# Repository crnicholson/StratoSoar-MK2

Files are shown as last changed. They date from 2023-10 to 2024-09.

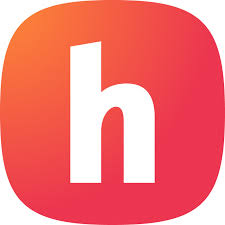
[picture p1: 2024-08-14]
Media/hack.jpeg

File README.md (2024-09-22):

# StratoSoar MK2 - UAVs For the Masses

<!-- **TL;DR**: The StratoSoar project is a low-cost, lightweight UAV designed to be dropped from a weather balloon  at any altitude, aiming for autonomous, efficient flight to selected GPS coordinates. The hope is to get a UAV platform in the hands of educators, researchers, and hobbyists alike since StratoSoar is much smaller, lighter, and cheaper than conventional UAVs.  -->

**TL:DR**: The StratoSoar project is a low-cost, lightweight Unmanned Aerial Vechile (UAV) designed for deployment from a weather balloon at various altitudes, aiming for autonomous and efficient flight to designated GPS coordinates. By offering a more affordable, compact, and lightweight alternative to conventional UAVs, StratoSoar aims to empower educators, researchers, and hobbyists with an accessible platform for exploration and experimentation. 

## Watch The Video

<!-- **WORK IN PROGRESS** - This project is still in the works. I don't recommend using it yet because it has the potential of being dangerous.

**NEW** - Writing code and making the PCB. 

**STATE as of 7/1/24** - Just starting development! -->

YouTube Video (https://www.youtube.com/watch?v=TiqkcGWG4g8&t=1s)

Glider | PCB
-- | --
<i>StratoSoar glider.</i> | <i>StratoSoar MK2.0 circuit board.</i>

## What Is the StratoSoar Project?

StratoSoar is a low-power, adaptive UAV that is dropped from a weather balloon at approximately 5,000 feet, with plans to reach even higher altitudes soon. The main goal of StratoSoar is to fly to selected GPS coordinates efficiently or choose a closer, more realistic landing site without human interaction. The current aim for StratoSoar is to operate on a single 600 mAh 15 gram LiPo battery for a 10+ hour flight. 

## Now, What Is a UAV?

UAVs, or Unmanned Aerial Vehicles, are autonomous aircraft, usually in the form of planes or drones. They have many applications, such as [delivering medicine, food, and supplies](https://www.flyzipline.com/) to remote areas, participating in aerial combat with the military, and conducting aerial imaging.

### Common Types of UAVs Include:

- Quadcopter (typical drones)
- Fixed-wing aircraft (like StratoSoar)

## StratoSoar vs. Conventional UAVs

### Traditional UAVs Are Typically:

- Large (5-15 meter wingspan)
- Heavy (2-20 kg)
- Expensive ($10,000-10,000,000 USD)
- Closed source and propietary

### StratoSoar Aims to Overcome These Limitations With:

- Weight: less than 250 grams
- Wingspan: 80 cm
- Cost: less than $150 USD
- Open source and accesible

## What Are the Uses of StratoSoar?

I'm currently considering two main concepts: an educational kit for students and hobbyists or a platform designed to study the aerodynamics of the stratosphere, a field with limited existing resources. Additionally, I'm exploring other ideas such as reusable radiosondes, systems for remote delivery of medicine and parcels, and advanced atmospheric monitoring solutions.

<!-- ## What Includes the StratoSoar Project? What Are the Different Parts of it?

StratoSoar has many different parts, and they all combine to make this project. 

- **Code** - All of the code directory, and the programs needed to run it. These include the main `.ino`s and the accompanying `.cpp` and `.h` files, along with the test files for the IMU and GPS.
- **PCB** - The circuit board is the basis of this project, it interfaces the code with the glider. StratoSoar includes the circuit board files and the schematics and everything needed to build a PCB.
- **3D Files** - StratoSoar requires some 3D printed parts to function, but these files also serve as an interactive build guide. StratoSoar includes the 3D files needed to print parts for the glider and the 3D files to assemble the glider.
- **Media** - The images and such of StratoSoar. 
- **Cutdown Mechanism** - This is the thing that helps you release the glider from the balloon payload - or whatever you want to drop it from. This includes all of the above things but will be in a separate GitHub repository.  -->

## How Does StratoSoar Work at a High Level?

<!-- StratoSoar is attached to a weather balloon via the cutdown mechanism. Once the balloon reaches the desired altitude, the cutdown mechanism drops the glider. The glider then descends, steering its way to specified coordinates. 

StratoSoar takes pride in being highly configurable and hackable, so there are many ways you change how it comes down built into the code. 

StratoSoar uses data from an IMU that goes through a Kalman filter to receive accurate AHRS, or Attitude Heading Reference System. This can tell StratoSoar the pitch, yaw, and roll of the glider. Then, StratoSoar integrates a GPS module to get the GPS coordinates. Both the GPS and the AHRS are used to compute the azimuth to find the turning angle of the glider. The turning angle tells the glider how much it needs to turn to be facing the correct yaw that will get the glider to the target location. Additionally, an algorithm is used to get the distance between the glider location's and the target location. 

With the turning angle computed, a PID mechanism is used to control the servo attached to the rudder of the glider. This PID mechanism learn from it's mistakes and can accurately aim the glider in the correct direction. 

Additionally, the glider beacons it's location at a configurable interval with LoRa for tracking. It also allows for a camera module to be added on to take photos and video. 

The glider will fly to the selected coordinates, and depending on the user configuration, will either spiral down or release a parachute above the coordinates once it has reached them to safely descend. Additionally, if the glider is too low in altitude, prior to the flight the user can enter closer coordinates as backup landing locations.  -->

StratoSoar MK2 is an advanced autonomous glider designed to operate at high altitudes, such as those reached by weather balloons. The glider is attached to a weather balloon via a cutdown mechanism. Once the balloon reaches the desired altitude, the cutdown mechanism releases the glider, initiating its descent. The glider then navigates autonomously to specified coordinates, using a combination of sensors, advanced algorithms, and low-power electronics.

### Core Components and Functionality:

- **Autopilot System**:
    - **GPS and IMU Integration**: StratoSoar uses a custom GPS module and an IMU, both designed for low-power operation. The IMU data is processed through a Kalman filter to provide accurate Attitude Heading Reference System (AHRS) data, including pitch, yaw, and roll. This information, combined with GPS coordinates, enables precise navigation.
    - **Servo Control with PID**: A PID control mechanism governs the rudder’s servo, ensuring precise adjustments to the glider's course based on real-time feedback.
    - **Hackability**: StratoSoar is designed to be highly configurable and hackable. Users can customize its descent strategy, whether by spiral descent, parachute deployment, or alternative landing locations. The codebase is modular, allowing for easy modifications or the addition of new features.
   
- **PCB Design**:
    - **StratoSoar MK3 PCB**: The main PCB, optimized for power efficiency, size, and cost, integrates over 100 components, managing the various systems onboard.
    - **Additional PCBs**: Supporting PCBs, such as those for the GPS module, switching regulator, and IMU, are designed for specific tasks, enhancing the glider's overall functionality.

### Operation and Recovery:

Upon release from the weather balloon, StratoSoar begins its guided descent following waypoints or single target coordinate. It calculates the optimal flight path using its GPS and AHRS data, making real-time adjustments to its trajectory through the PID-controlled servo system. Depending on user configurations, the glider can either glide smoothly to the target coordinates, initiate a spiral descent, or deploy a parachute for a safe landing.

If the glider's altitude drops below a certain threshold, backup landing coordinates can be used to ensure a safe recovery. Throughout the flight, the glider’s location is continuously transmitted, allowing for easy tracking and recovery.

<!-- ## File System and More Project Info

I'm only listing the key items, leaving out all the unessecary stuff. This should give you a general sense of the project and all it's features. Note that this is also only stuff I did during Hack Club Arcade.

- `Code/autopilot`: (5000 lines of code!)
    - `autopilot.ino`: The script that ties all of these files together.
    - `gps.cpp`: GPS code custom-made for low-power.
    - `waypoint.cpp`: Custom waypoint flight with advanced turning.
    - `lora.cpp`: LoRa communications with complex forward error correction.
    - `sd.cpp` + `eeprom.cpp`: Data logging in a low-power manner.
    - `servo.cpp`: Ultra low-power servo functions.
    - `bme280.cpp`: Weather data sensor.
    - `imu.cpp`: An interial measurement unit running a Kalman filter.
- `Code/groundStation`: 
    - `groundStation.ino`: The code for the receiving station of the LoRa telemetry, uses ESP32 and HTTP requests to communicate with the server, also locally logs data. 
    - `uploader/flaskUploader.py`: A Flask server that uses an API to put all the data on SondeHub. 
- `Code/camera`: Utilization of a low-power camera module and Python scripts for conversion.
- `Code/calculator`: Python script to parametrically create flying wing glider. 
- `PCB/StratoSoar-MK3.0`: The main PCB consisting of over 100 components, optimized for power, size, and cost.
- `PCB/gpsBreakout`: A PCB designed for testing a cheap, $2 Chinese GPS module.
- `PCB/loRa`: The ground station to receive the glider's data. 
- `PCB/camera`: A breakout board for a low-power camera module. 
- `PCB/imuBreakout`: One of the first breakout boards made for a new Interial Measurement Unit. 
- `3D Files/cardboardGlider`: Parametric Fusion 360 desgin for a folding origami glider. 
- `3D Files/StratoSoar Rev2 v36`: High efficieny glider. -->

## A Quick Note on MK1, MK2, Naming, and Revisions

StratoSoar MK1 was the precursor and the spark to StratoSoar MK2. StratoSoar MK1 was officially developed from October 1st to July 30th, although StratoSoar MK2 was unofficially being worked on in the months of March through June. StratoSoar MK1 failed to fly autonomously, and it also failed to release from the balloon. Major upgrades have been made since then.

StratoSoar MK2 officially started on October 1st, and has now ended. It was a success. 

My newer version, which you should check out, officially started on June 1st. It is called StratoSoar MK3 and will end in quite some time when I launch it from a weather balloon. A new major revision (eg. MK4) will come out every time when I release the glider from the balloon in the Summer. After the Summer, work on the next revision begins, with many updates and new features. 

<!-- A new sub-revision (for lack of better word) comes out every time I make a new PCB. For example, my first version of my PCB was MK2.0. At the time of writing, the current version of StratoSoar is MK2.1. A new version of 3D model is denoted by the Rev number. Rev starts at 0. 0 and 1 are not shown in this repo because they didn't turn out very good. The physical gliders are denoted by the 3D model number. Sometimes a small change is made with glider so the name of the glider is Rev x.x, for example. Sometimes the same happens with the 3D model, again it would be x.x. To put this in practice, the final glider may be MK2.5 Rev 7.3.1. The code has no version history in the way the 3D models and the PCB do. -->

Also, I use "we" a lot in this writing. This usually refers to myself or this project, but it also refers to my small team over at New England Weather Balloon Society.

One last thing. When I refer to StratoSoar, I am referring to the project as a whole, but more specifically, the most recent version. 

<!-- ## Watch my Talk About StratoSoar MK2 The North East HamXpo! -->

## Is This Legal?
Yes! During flight, the ground operator has no ***direct*** control over the flight path, i.e. via a radio. Because of this, and it being unpowered, it qualifies as a free flight glider. Free flight gliders have very little regulations. You can think of them as a paper airplane. 

## Can I Buy a Kit or a Complete Product?

Currently, StratoSoar is not available to purchase online as a kit or complete product. We have plans in the next few years to release a kit for schools, education centers, hobbyists and a complete product for industry at an affordable price. You are welcome to make one in the mean time!

## How Can I Make One? Are There Docs?

One of the goals of StratoSoar was to make an affordable and open source system for anyone to perform stratospheric research, so all the files are available for free. This means that you can construct StratoSoar from scratch. **A guide to do this will be available soon.**

<!-- It is still in the works, but you can check out `DOCS.md` under the `Docs` folder.**  -->

## Helpful Sources and Credits

I'm in the midst of compiling this.

## Cutdown Mechanism

[See my other WIP GitHub repo.](https://github.com/crnicholson/Cutdown-Mechanism)

## Funding and Support

We currently have <u>**very**</u> limited funding to complete this project. We would **love any donations or sponsorships** we could get to elevate (no pun intended) this project to the next level. If you don't want to donate, but want to help out, we would love your support with other areas of this project. Reach out to me if you have interest at:

- [newbsballoons@gmail.com](mailto:newbsballoons@gmail.com) (organization email, recommended).

- [charlienicholsonr@gmail.com](mailto:charlienicholsonr@gmail.com) (personal email).

## Special Thanks

This project would not be possible without the following individuals:

- Max Kendall (W0MXX) for working closely together with me.

- Mike Malis for helping with the design of the glider. 

- Brett Miwa for schematic review, PCB design, electrical theory, and boost converter circuitry design.

- Bob Phinney (K5TEC) for providing NEST and securing funding.

- Mark Jessop (VK5QI) for answering all of my questions.

- Mike Hojnowski (KD2EAT) for PCB design and hardware/software debugging.

- Paul Hamilton for helping me with FAA regulations.

- My parents!

And these entities:

- Hack Club, for providing support for projects like this. 

- New England Sci-Tech (NEST) for providing a maker space to work, funding, and hosting NEWBS.

- New England Weather Balloon Society (NEWBS) for expertise and the opportunity.

- Bagel Fund, for providing funding. 

## Affiliate Programs and Projects

- **Hack Club** - Hack Club is a non-profit designed for teenagers that provides support for projects like this. 
- **NEWBS** - Max and Seth Kendall of NEWBS, or New England Weather Balloon Society, are helping me launch my project from a balloon. They are dedicated to helping people in New England launch weather balloons. 
- **New England Sci-Tech** - Bob Phinney of NEST is hosting NEWBS. NEST is a great maker space. If you are in the Greater Boston Area, go check them out!
- **StratoScience** - This is the official class that I'm in helping me launch my project. This is a high altitude engineering class for teens. Check them out if your are in the Greater Boston area!

## Still Have Questions?

Do you have any questions? Are the docs incomplete and you want to ask anything? Do you just want to say hi (or how cool my project is!)?

Reach out to me at [charlienicholsonr@gmail.com](mailto:charlienicholsonr@gmail.com).

## License

Both the software and documentation are under the [GNU GPL v3 license](https://choosealicense.com/licenses/gpl-3.0/). The hardware and the 3D files are under the [CERN Open Hardware Licence Version 2 - Strongly Reciprocal](https://choosealicense.com/licenses/cern-ohl-s-2.0/). The media is under the [CC BY 4.0 DEED](https://creativecommons.org/licenses/by/4.0/).

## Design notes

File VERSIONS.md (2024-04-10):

## Version History

A quick little summary of the versions and what worked and what didn't, plus what was changed between revisions.

PCBs:
- StratoSoar MK2.0 - First attempt, many issues. Wrong LDO, transistor, and TCXO footprint. Boost converter did not work. Reset button did not work. Main sketch works along with mostly everything else. Missing silkscreen designators and numerous cosmetic problems. GPS untested. IMU untested.
- StratoSoar MK2.1 - Success!

Gliders/3D models:
- Rev 0 - Never flew, bad design.
- Rev 1 - Built and tested, horrible design.
- Rev 2 - Currently constructing this.

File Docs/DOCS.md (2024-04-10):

# StratoSoar Docs - A Work in Progress!

This is split into a few different sections to be more organized. These are as follows:

- General
- PCB
- Code and Programming
- Glider
- Usage

# General

## StratoSoar File Layout

## Power Consumption

# PCB

## Required Parts for the PCB

<!--

**NOTE:** Incomplete, more to come soon.

This codebase is meant to work with the StratoSoar PCB, also on this GitHub repository. On it are these basic components:

-  **Microcontroller** - [SAMD21G18A](https://www.microchip.com/en-us/product/atsamd21g18). This is a modern Cortex-M0 microcontroller by Microchip. It runs on ARM and has low-power capabilities.

-  **GPS Module** - [MAX-M10S](https://www.u-blox.com/en/product/max-m10-series). This is a top-of-the-line GPS module from u-blox.

-  **Environmental Sensor** - [BME280](https://www.bosch-sensortec.com/products/environmental-sensors/humidity-sensors-bme280/). This is a sensor from Bosch proven to work on HAB flights. Measures temperature, pressure, and humidity.

-  **Boost Converter** - [TPS61200](https://www.ti.com/product/TPS61200). This is a boost converter from Texas Instruments. This is used to convert from 1.5v (or 3v with two batteries) to 5v for the servos. The output of this is hooked up to the input of the LDO.

-  **LDO Step-Down Regulator** - [MCP1700](https://www.microchip.com/en-us/product/mcp1700). This is 5v to 3.3v low-dropout and low-quiescent current voltage regulator, supplying everything besides the servos.

-  **Internal Measurement Unit (IMU)** - [MPU-9250](https://invensense.tdk.com/products/motion-tracking/9-axis/mpu-9250/). This little device is an accelormeter, gyroscope, and magnetometer all-in-one that can be used to find pitch, roll, and yaw among other metrics.

This list is not at all comprehensive, but it features the basic components. Check out the schematic for more!
-->

## PCB Assembly

## PCB Configuration

**NOTE:** This is only relevant for MK2.1 and upwards.

Jumpers:
- **JP1**: Solder to enable PPS LED of GPS module.
- **JP2**: Solder to enable one cell battery operation. Default is two cell battery operation. 
- **JP3**: Solder to enable pin 13 ATMega LED. 
- **JP4**: Solder to enable SAMD error LED.
- **JP5**: Solder to enable SAMD pin 13 LED. 
- **JP6 + JP7**: Solder to enable external 32.768 kHz crystal. Note that the crystal must be soldered and enabled if the TCXO is not placed. 

Switches:
- **SW2**: Switch towards the GPS module to disable EEPROM. Switch away to enable EEPROM.
- **SW3**: Switch towards the GPS module to supply power via the PCB-mounted batteries. 

## PCB Headers and Interfaces 

# Code and Programming

## Code Structure and Layout

## Code Configuration

## Setting up Microchip Studio for Bootloader Programming with J Link

## Setting up Arduino IDE

<!--

**NOTE:** Incomplete, more to come soon.

This project is based on the Arduino IDE workflow. Below steps outline steps necessary to install Arduino IDE and configure it for the SAMD microcontroller.

1. Install [Arduino IDE](https://www.arduino.cc/en/software) from [here](https://www.arduino.cc/en/software).

2. [Download the Arduino SAMD core](https://docs.arduino.cc/learn/starting-guide/cores/).

3. Download necessary libraries from library manager:

a. ArduinoLowPower

c. Sparkfun GNSS v3

5. To following needs to be downloaded directly from GitHub:

a. TinyBME280

4. Open Tiny4FSK.ino by double-clicking it (should open Arduino IDE).

The SAMD goes to sleep to save power. To achieve proper sleep, some edits to the SAMD core are necessary. To find the wiring.c file on your computer, [follow this guide](https:support.arduino.cc/hc/en-us/articles/4415103213714-Find-sketches-libraries-board-cores-and-other-files-on-your-computer).

Once there, comment out or completely delete this line as shown:

#ifndef VERY_LOW_POWER

// Setup all pins (digital and analog) in INPUT mode (default is nothing)

for (uint32_t ul = 0 ; ul < NUM_DIGITAL_PINS ; ul++ )

{

pinMode( ul, INPUT ) ;

}

#endif

**NOTE: ** Arduino gives you an official warning:

> This breaks Arduino APIs since all pins are considered INPUT at startup. However, it really lowers the power consumption by a factor of 20 in low power mode (0.03mA vs 0.6mA).

>

Though from testing, there do not seem to be any performance issues.
-->

# Glider

## Required Parts for the Physical Glider

## Printing the Parts

## Making the Wing

## Making the Fuselage

## Making the Control Surfaces

## Assembling Everything

# Usage

## Power-on Cycle

## How to Actually Use in a Flight

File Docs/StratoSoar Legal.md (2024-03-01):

<!-----
Note to self:
GitHub uses a different Markdown engine than StackEdit, so stuff compiles differently. For example, you need an empty line after a bold to make the bold text not appear on the same line as the other text. 

Also, tables don't compile well.
----->

Charles Nicholson<br>
[charlienicholsonr@gmail.com](mailto:charlienicholsonr@gmail.com)<br>
March 1st, 2024<br>

# StratoSoar Legal Information
**Disclaimer: I am by no means a lawyer.**

## Overview

[StratoSoar](https://github.com/crnicholson/StratoSoar-MK2/) is an open source project that uses three different licenses, the GNU GPL v3 license, the CERN license, and the CC BY license. This article will outline the legal protection of StratoSoar and hopefully will help you in licensing and protecting your open source work. 

## StratoSoar’s Future

I have dreamed of making StratoSoar an educational tool at a low-cost for classrooms and hobbyists. This means making a simple kit available for people to construct, modify, and program to do stratospheric aviation, opening a whole new unexplored part of the world for citizen science. This kit and code would be simple enough for anyone to build it and understand it, leaving space for open source modifications. The source for this will always be free and the kit will always be cheap.

The other pathway will be making StratoSoar a commercial product. This would be something the NWS or atmospheric centers buy to conduct research. I have also discussed making this a replacement for radiosondes. The commercial use cases are endless, but in any commercial setting, it is unlikely the NWS (or other companies) wants something they use for research being open source. So this means making two different projects and products at some point down the line. There would be one closed source and one open source project, with the closed source being more advanced. Currently, and probably for the next few years, I will be working on the open source StratoSoar. Working on the less-advanced open source StratoSoar means that I don’t have to worry as much about the future and selling StratoSoar because eventually StratoSoar will go two ways, leaving more time to make an awesome project without many limitations for you guys. That being said, I still want protection for StratoSoar, which is what this article is about.

## Trademark

Trademark is primarily made for consumer protection, protecting against brands in the same industry using the same logo confusing a consumer. A trademark is a brand’s logo, slogan, set of colors, or name, to list a few. A scissors company can use a similar logo as a tennis company, because they are totally different industries. 

StratoSoar, the glider, does not have a registered trademark (Ⓡ). Registering a trademark costs upwards of $250. On the other hand, you can use an [unregistered trademark](https://en.wikipedia.org/wiki/Unregistered_trademark) for free in your geographical location by using the ™ character. This has less rights. For example, if a business or project in my geographical area wanted was using StratoSoar as a name, and I had started using it before them, I would have a small but fighting chance of winning in court. 

StratoSoar will not be using an unregistered trademark because I want this to be easy for you all to replicate and use. 

If you want some added protection for your logo without using a trademark, that is available at no extra cost to you. As further discussed in the next section, copyright already protects the logo. Not trademarking the logo because it’s already copyrighted is well explained [here](https://law.stackexchange.com/questions/31444/why-register-a-logo-as-trademark-if-copyright-protects-it). 

> **Fun Fact**<br>
> Software licenses allow for trademarked logos, names, etc. simply because the license is licensing the code, not the name or the rest of the project. 

The name StratoSoar has previously been trademarked, but the trademark was put into action in 2012, and trademarks need renewal every 10 years. The trademark on the name lapsed. Besides, the trademark was for a [roller coaster](https://newsplusnotes.blogspot.com/2010/08/all-way-up-into-stratosoar.html), which is a completely different field than UAVs, so StratoSoar as a name still could be registered back in the 2010s. 

## Copyright

A copyright is automatically produced whenever you create IP (intellectual property). This includes something like artwork, code, and writing, but not something useful (hardware). It protects someone copying your work (and possibly adding modifications) then releasing it as their own. It allows someone to distribute their work in a safe manner for themselves. 

StratoSoar has a copyright on its entire GitHub repository. This includes the Code, PCB + Schematic (not as much here, this can iffy), 3D Files, Media, and Docs. I choose to give away some of my rights by using an open source license, more on that later.

## License

I chose to add an open-source license to the StratoSoar project so other people could legally use my code. Without a license, generally nobody else can use, copy, distribute, or modify your work without being at risk of take-downs, shake-downs, or litigation. A license, in a way, is a legal document that explicitly gives rights to the user to do what the license permits. There are two main types of open-source licenses, copy-left and permissive. Copy-left means that any changes must be redistributed using the same license. Permissive doesn’t care what you do with it when you edit it and release it. 

There are many different licenses you can choose from, ranging from software to hardware to media licenses. UPDATE THIS. Generally, binary compilations and source code are considered software. Hardware has a broader definition, but usually it includes PCBs, physical products, schematics, 3D design files, STLs, Gerbers, source/design files for something physical, and compiled files for something physical. Media is usually considered artistic work, logos, and images. Documentation is usually covered by the software license. 

There are many different types of licenses for open-source projects, mostly consisting of software licenses, with it being the most popular and having the most support. Websites like [Choose Your License](https://choosealicense.com/) will guide you to choosing the correct license for your use case. Websites like this [open source guide](https://opensource.guide/legal/) will help you further in understanding the law and regulations of open source. 

> **Fun Fact**<br>
> You can change most software licenses IF you are the sole contributor. If not the sole contributor, it can become more complicated. 

## Software Licensing

There are two main types of software licenses, GNU GPL v3 and MIT. MIT is very permissive and GPL is very copy-left. Here are the main comparisons between them:

<table>
  <tr>
   <td>License
   </td>
   <td>Permissions
   </td>
   <td>Conditions 
   </td>
   <td>Limitations
   </td>
  </tr>
  <tr>
   <td>GNU GPL v3
   </td>
   <td>
<ul>

<li>Commercial use

<li>Distribution 

<li>Modification

<li>Patent use

<li>Private use (modifications don’t have to be disclosed if product is not publicly distributed)
</li>
</ul>
   </td>
   <td>
<ul>

<li>Source code must be made available if product is distributed to the public

<li>License and copyright notice must be included with the product and the source code (this is a way to give attribution to the original author)

<li>Modifications must be licensed under the same license

<li>Changes to the licensed material must be stated 
</li>
</ul>
   </td>
   <td>
<ul>

<li>There is a limitation of liability

<li>There is NO warranty
</li>
</ul>
   </td>
  </tr>
  <tr>
   <td>MIT
   </td>
   <td>
<ul>

<li>Commercial use 

<li>Distribution

<li>Modification

<li>Private use
</li>
</ul>
   </td>
   <td>
<ul>

<li>License and copyright notice must be included with the product and the source code 
</li>
</ul>
   </td>
   <td>
<ul>

<li>There is a limitation of liability

<li>There is NO warranty
</li>
</ul>
   </td>
  </tr>
</table>

> **Beware**<br>
> Creative Common (CC) licenses should not be used to license software or hardware. CC licenses are good for everything else, including docs (usually covered by the software license)

> **Fun Fact**<br>
> Almost all software licenses (including GPL v3 and MIT) offer licensing for documentation of any type.

> **Fun Fact**<br>
> The MIT license is compatible with the GNU GPL v3 license, but not vice versa. 

> **Fun Fact**<br>
> Under the GPL v3 license, you don't need to release source code to the public if you modify it and you use it commercially inside your own company. This means that StratoSoar can make changes and not disclose them to the public (don't worry, I won't do that). See the full list of GPL v3 FAQs here. 

Currently, StratoSoar is under an MIT software license. I am oscillating between a GPL and an MIT license. As discussed in the beginning, I don’t plan on selling StratoSoar. But, if I did, it wouldn’t matter what license I use because both allow for private use of the software inside a company. 

There are a few reasons I may switch to GPL v3. If anyone decides to rip me off and sell StratoSoar as a kit, they will have to release their code to the public and people will see that I’m the real owner. In another scenario, if someone used and modified my code in flight and wanted to post it on GitHub, they would need to link to my project. Essentially, GPL v3 gives me as the owner more protection. 

**Edit**: I’ve switched over to GPL v3. I’m keeping the above section in case it’s helpful to you. 

Here are some more examples. Using the GPL v3 or MIT license, if someone modified my code but did not sell it and only used it on a flight they would not need to share the code to the public. Using the GPL license, if they modified the code, and sold a DIY kit shipped with the program pre-programmed, source code would need to be distributed and credit would be given to me. This is different using the MIT license, no source code or credit would be needed, which isn’t very cool. 

## Using and Implementing the Software License

I found actually using the license to be a bit more difficult. For the MIT license, you only need to include the license in one part of the your code directory, often labeled as LICENSE.txt or LICENSE.md, though it is considered good practice to include something along the lines of a copyright notice and saying that the code is licensed under the MIT license in every source code file. GPL v3 can be more annoying, as it requires you to have a segment of the license in every source code file. The segment, and a little disclaimer, can be found at line 629 of the license. You also need to include the full license, though only once in the directory, again usually as LICENSE.txt or LICENSE.md. See [my code](https://github.com/crnicholson/StratoSoar-MK2/blob/main/Code/Autopilots/autopilot/autopilot.ino) for an example. 

## Hardware Licensing

I’m still waiting to hear back from OSHWA to know what is actually defined as hardware. Right now, I believe it is everything physical and all design files required to make that physical thing. These may include STLs, PCBs, schematics, Gerbers, etc.

There is basically only one license you want to use for open source hardware, because the license comes in different forms. This license is called the CERN Open Hardware License. The three different forms of the CERN are the [CERN Open Hardware Licence Version 2 - Permissive](https://choosealicense.com/licenses/cern-ohl-p-2.0/), the [CERN Open Hardware Licence Version 2 - Weakly Reciprocal](https://choosealicense.com/licenses/cern-ohl-w-2.0/), and the [CERN Open Hardware Licence Version 2 - Strongly Reciprocal](https://choosealicense.com/licenses/cern-ohl-s-2.0/). The definition of reciprocal is similar to copyleft in software licenses. We will be covering the strongly reciprocal and the permissive CERN licenses. 

<table>
  <tr>
   <td>License
   </td>
   <td>Permissions
   </td>
   <td>Conditions 
   </td>
   <td>Limitations
   </td>
  </tr>
  <tr>
   <td>CERN Permissive
   </td>
   <td>
<ul>

<li>Commercial use

<li>Distribution 

<li>Modification

<li>Patent use

<li>Private use (modifications don’t have to be disclosed if product is not publicly  distributed)
</li>
</ul>
   </td>
   <td>
<ul>

<li>License and copyright notice must be included with the design files

<li>Changes to the design files must be stated 
</li>
</ul>
   </td>
   <td>
<ul>

<li>There is a limitation of liability

<li>There is NO warranty
</li>
</ul>
   </td>
  </tr>
  <tr>
   <td>CERN Strongly Reciprocal
   </td>
   <td>
<ul>

<li>Commercial use

<li>Distribution 

<li>Modification

<li>Patent use

<li>Private use 
</li>
</ul>
   </td>
   <td>
<ul>

<li>License and copyright notice must be included with the design files

<li>Design files must be made available if product is distributed to the public

<li>Modifications must be licensed under the same license

<li>Changes to the licensed material must be stated 
</li>
</ul>
   </td>
   <td>
<ul>

<li>There is a limitation of liability

<li>There is NO warranty
</li>
</ul>
   </td>
  </tr>
</table>

StratoSoar uses the CERN Strongly Reciprocal OHL.

## Using and Implementing the Hardware License

To use a CERN license, simply include the license once in the root directory. 

## Media/Photo Licensing 

StratoSoar has licensed its media under the [Creative Commons Attribution 4.0 International license](https://choosealicense.com/licenses/cc-by-4.0/). This is the one of the most common open source licenses for anything besides software and hardware, and it will be the only I’ll be covering. 

<table>
  <tr>
   <td>License
   </td>
   <td>Permissions
   </td>
   <td>Conditions 
   </td>
   <td>Limitations
   </td>
  </tr>
  <tr>
   <td>CC BY 4.0
   </td>
   <td>
<ul>

<li>Commercial use

<li>Distribution 

<li>Modification

<li>Private use (modifications don’t have to be disclosed if product is not publicly  distributed)
</li>
</ul>
   </td>
   <td>
<ul>

<li>License and copyright notice must be included with the design files

<li>Changes to the design files must be stated 
</li>
</ul>
   </td>
   <td>
<ul>

<li>There is a limitation of liability

<li>There is NO warranty

<li>No patent use

<li>No trademark use
</li>
</ul>
   </td>
  </tr>
</table>

There are a plethora of other Creative Commons licenses out there, this is just one of the most open and recommended ones. 

## Using and Implementing the Media License

To use the CC license, you should add a little snippet to your media directory, like shown:

```
Copyright 2024 Charles Nicholson 

This work is licensed under a CC BY 4.0 DEED International License.
https://creativecommons.org/licenses/by/4.0/.
```

## Documentation Licensing

You often don’t need to worry about licensing your documentation because the software license usually covers that. If it didn’t, I would use the above CC BY license used for media. 

## Quick Tips

* I like to spell StratoSoar as StratoSoar, not Stratosoar, but this doesn't mean anything in court because trademarks are generally not case sensitive. 
* Open source is not one word like opensource. If you're writing it as a noun, you should not use a hyphen. As an adjective, you _can_ use a hyphen to clarify that it's a single compound adjective, if there's a danger of confusion. You should not capitalize the O unless you are referring to OSI. 
* Source code is all the code that exists BEFORE getting compiled into binary that a machine can read.

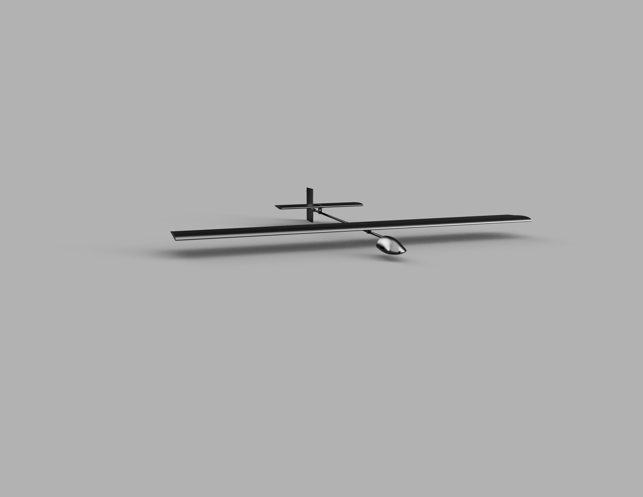
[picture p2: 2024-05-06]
PCB + Schematic/StratoSoar-MK2.2/niceRender.PNG

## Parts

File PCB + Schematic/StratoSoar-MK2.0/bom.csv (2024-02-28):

Designator | Footprint | Quantity | Value | LCSC Part #
AE1 | RAINSUN_GPS1003 | 1 | Antenna_Chip
BT1, BT2 | BatteryHolder_BK-82 | 2 | AAA
C1, C11, C13, C16, C18, C23, C26, C7, C9 | 0805 | 9 | 100nF
C10, C15, C22, C4 | 0805 | 4 | 10uF
C12 | 0805 | 1 | 1 uF (BT1)
C14 | 0805 | 1 | 100 nF (XTAL1)
C17 | 0805 | 1 | 1uF
C19 | 0805 | 1 | 100 pF (XTAL1)
C2 | 0805 | 1 | 10 nF (U2)
C20, C21 | 0805 | 2 | 100 nF (J1)
C24, C25 | 0805 | 2 | 1 uF (U1)
C27, C33 | 1206 | 2 | 100nF (U7)
C28 | 1206 | 1 | 22uF (U7)
C29 | 0805 | 1 | 100nF (U7)
C3, C5 | 0805 | 2 | 22pF
C30 | 1210 | 1 | 47uF (J10)
C31 | 1210 | 1 | 47uF (J7)
C32 | 1210 | 1 | 47uF (J9)
C34 | 1206 | 1 | 10uF (U7)
C6 | 0805 | 1 | 100 nF (U2)
C8 | 0805 | 1 | 1nF
D1, D4 | 0805 | 2 | LED
D2 | 0805 | 1 | AT_LED
D3 | 0805 | 1 | ERR_LED
FB1 | 0603 | 1 | BLM18AG121SN1D (J1)
H1, H2, H3, H4 | MountingHole_2.2mm_M2 | 4 | MountingHole
J1 | PinHeader_1x04_P2.54mm_Vertical | 1 | BME280
J10 | PinHeader_1x03_P2.54mm_Vertical | 1 | parachute
J2 | PinHeader_2x03_P2.54mm_Vertical | 1 | AT_ISP
J3 | PinHeader_1x11_P2.54mm_Vertical | 1 | Signal
J4 | PinHeader_1x04_P2.54mm_Vertical | 1 | AT_FTDI
J5 | USB_C_Receptacle_GCT_USB4105-xx-A_16P_TopMnt_Horizontal | 1 | USB_C_Receptacle_USB2.0
J6 | PinHeader_1x05_P2.54mm_Vertical | 1 | JTAG
J7 | PinHeader_1x05_P2.54mm_Vertical | 1 | Power
J8 | PinHeader_1x03_P2.54mm_Vertical | 1 | rudder
J9 | PinHeader_1x03_P2.54mm_Vertical | 1 | elevator
JP1 | SolderJumper-2_P1.3mm_Bridged_RoundedPad1.0x1.5mm | 1 | PPS_EN
JP2 | SolderJumper-2_P1.3mm_Bridged_RoundedPad1.0x1.5mm | 1 | ONE_CELL
JP3 | SolderJumper-2_P1.3mm_Bridged_RoundedPad1.0x1.5mm | 1 | AT_LED_EN
JP4 | SolderJumper-2_P1.3mm_Bridged_RoundedPad1.0x1.5mm | 1 | ERR_LED_EN
JP5 | SolderJumper-2_P1.3mm_Bridged_RoundedPad1.0x1.5mm | 1 | LED_EN
JP6 | SolderJumper-3_P1.3mm_Bridged12_RoundedPad1.0x1.5mm | 1 | PS_EN
L1 | 0805 | 1 | 33nH
L2 | 0805 | 1 | 10uH
L3 | IND_LPS3015 | 1 | LPS3015-222ML
Q1, Q2, Q3 | SOT-23_Handsoldering | 3 | 2N3906
Q4, Q5, Q6 | SC-59_Handsoldering | 3 | DMN1019USN-13
R1, R11, R12, R5 | 0805 | 4 | 1K
R10, R7, R8, R9 | 0805 | 4 | 1.8K
R13, R15, R16, R17, R18, R22, R24, R4 | 0805 | 8 | 10K
R14, R21, R23 | 0805 | 3 | 10
R19 | 0805 | 1 | 91K
R2, R3 | 0805 | 2 | 1M
R20 | 0805 | 1 | 820K
R6 | 0805 | 1 | 5.1 K (J1)
SW1 | SW_SPDT_PCM12 | 1 | EEPROM
SW2 | SW_SPST_CK_RS282G05A3 | 1 | AT_RESET
SW3 | SW_SPDT_PCM12 | 1 | AAA
SW4 | SW_SPDT_PCM12 | 1 | PWR_SW
SW5 | SW_SPST_CK_RS282G05A3 | 1 | RESET
U1 | InvenSense_QFN-24_3x3mm_P0.4mm | 1 | MPU-9250
U2 | ublox_MAX | 1 | MAX-M10S
U3 | TQFP-32_7x7mm_P0.8mm | 1 | ATmega328P-A
U4 | SOIC-8_3.9x4.9mm_P1.27mm | 1 | AT24C512C-SSHD-T
U5 | TQFP-48_7x7mm_P0.5mm | 1 | ATSAMD21G18A-A
U6 | SOT-89-3_Handsoldering | 1 | MCP1700x-330xxTT
U7 | Texas_S-PVSON-N10_ThermalVias | 1 | TPS61200DRC
XTAL1 | BGA4_SiT1532_SIT | 1 | SIT1552AI-JF-DCC-32.768D
Y1 | Crystal_HC18-U_Vertical | 1 | 8MHz
Y2 | ECS801033CHNTR | 1 | ECS-80-10

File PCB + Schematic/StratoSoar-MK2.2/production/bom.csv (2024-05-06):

Designator | Footprint | Quantity | Value | LCSC Part #
AE1 | ANT_1575AT_JOT-L | 1 | 1575AT43A0040001E
BT1, BT2 | BatteryHolder_BK-82 | 2 | AAA
C1, C11, C15, C16, C17, C19, C21, C22, C23, C25, C29, C3, C6, C8 | 0805 | 14 | 100nF
C10, C18, C26, C4 | 0805 | 4 | 10uF
C12, C20, C27, C28 | 0805 | 4 | 1uF
C13, C14, C7, C9 | 0805 | 4 | 22pF
C2 | 0805 | 1 | 10nF
C24 | 0805 | 1 | 100pF
C30, C31, C32 | CP_EIA-3528-21_Kemet-B | 3 | 47uF
C5 | 0805 | 1 | 1nF
D1, D4 | 0805 | 2 | LED
D2 | 0805 | 1 | AT_LED
D3 | 0805 | 1 | ERR_LED
FB1 | 0603 | 1 | BLM18AG121SN1D
H1, H2, H3, H4 | MountingHole_2.2mm_M2 | 4 | MountingHole
J1 | PinHeader_1x04_P2.54mm_Vertical | 1 | BME280
J10 | PinHeader_1x03_P2.54mm_Vertical | 1 | Rudder
J11 | PinHeader_1x03_P2.54mm_Vertical | 1 | Elevator
J12 | PinHeader_1x03_P2.54mm_Vertical | 1 | Parachute
J13 | 1x08_SMD_Pads | 1 | GY-91
J14 | 1x02_SMD_Pads | 1 | VOUT
J15 | 1x02_SMD_Pads | 1 | VIN
J2 | PinHeader_1x06_P2.54mm_Vertical | 1 | FTDI
J3 | PinHeader_2x03_P2.54mm_Vertical | 1 | AT_ISP
J4 | PinHeader_1x11_P2.54mm_Vertical | 1 | Signal
J5 | USB_C_Receptacle_GCT_USB4105-xx-A_16P_TopMnt_Horizontal | 1 | USB-C
J6 | PinHeader_1x05_P2.54mm_Vertical | 1 | SWD
J7 | PinHeader_1x05_P2.54mm_Vertical | 1 | Power
J8 | PinHeader_1x02_P2.54mm_Vertical | 1 | Button
J9 | PinHeader_1x02_P2.54mm_Vertical | 1 | VIN
JP1 | SolderJumper-2_P1.3mm_Open_RoundedPad1.0x1.5mm | 1 | PPS_EN
JP10, JP9 | SolderJumper-2_P1.3mm_Open_RoundedPad1.0x1.5mm | 2 | XO_EN
JP3 | SolderJumper-2_P1.3mm_Open_RoundedPad1.0x1.5mm | 1 | ONE_CELL
JP4 | SolderJumper-2_P1.3mm_Open_RoundedPad1.0x1.5mm | 1 | AT_LED_EN
JP5 | SolderJumper-2_P1.3mm_Open_RoundedPad1.0x1.5mm | 1 | ERR_LED_EN
JP6 | SolderJumper-2_P1.3mm_Open_RoundedPad1.0x1.5mm | 1 | LED_EN
L1 | 0805 | 1 | 33nH
L2 | 0805 | 1 | 10uH
Q1, Q2, Q3 | SOT-23-3 | 3 | 2N3906
Q4, Q5, Q6 | SC-59_Handsoldering | 3 | DMN1019USN-13
R1, R11, R13, R5 | 0805 | 4 | 1K
R10, R6, R7, R9 | 0805 | 4 | 1.8K
R12, R8 | 0805 | 2 | 5.1K
R14, R4 | 0805 | 2 | 220
R15, R16, R17, R18, R19, R20 | 0805 | 6 | 10K
R2, R3 | 0805 | 2 | 1M
R21, R22, R23 | 0805 | 3 | 10
SW1 | SW_SPST_CK_RS282G05A3 | 1 | AT_RESET
SW2 | SW_SPDT_PCM12 | 1 | EEPROM
SW3 | SW_SPDT_PCM12 | 1 | AAA
SW4 | SW_SPDT_PCM12 | 1 | PWR_SW
SW5 | SW_SPST_CK_RS282G05A3 | 1 | RESET
U1 | ublox_MAX | 1 | MAX-M10S
U2 | InvenSense_QFN-24_3x3mm_P0.4mm | 1 | MPU-9250
U3 | TQFP-32_7x7mm_P0.8mm | 1 | ATmega328P-A
U4 | SOIC-8_3.9x4.9mm_P1.27mm | 1 | AT24C512C-SSHD-T
U5 | Crystal_SMD_Abracon_ABM8AIG-4Pin_3.2x2.5mm | 1 | ATXK-H11-E-32.768
U6 | TQFP-48_7x7mm_P0.5mm | 1 | ATSAMD21G18A-A
U7 | SOT-89-3 | 1 | MCP1700x-330xxTT
Y1 | Crystal_HC18-U_Vertical | 1 | 8MHz
Y2 | Crystal_C26-LF_D2.1mm_L6.5mm_Horizontal | 1 | 32.768kHz

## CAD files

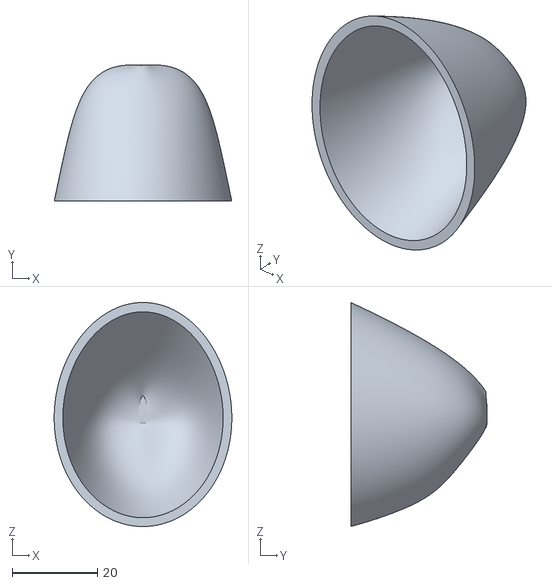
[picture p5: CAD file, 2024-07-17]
3D Files/noseCone.stl
41.7 x 32.0 x 52.5

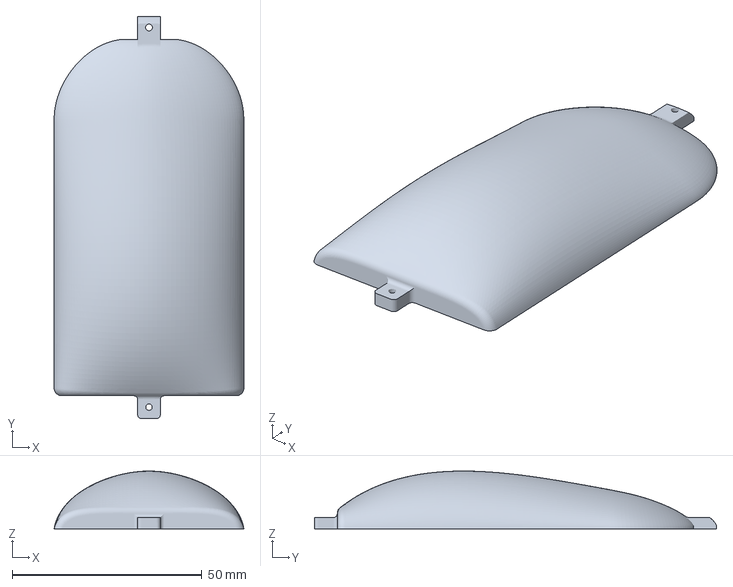
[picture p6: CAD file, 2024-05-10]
3D Files/objs 5:10:24/StratoSoar Rev2 v26 Cockpit.3mf
50.0 x 105.9 x 15.2 mm

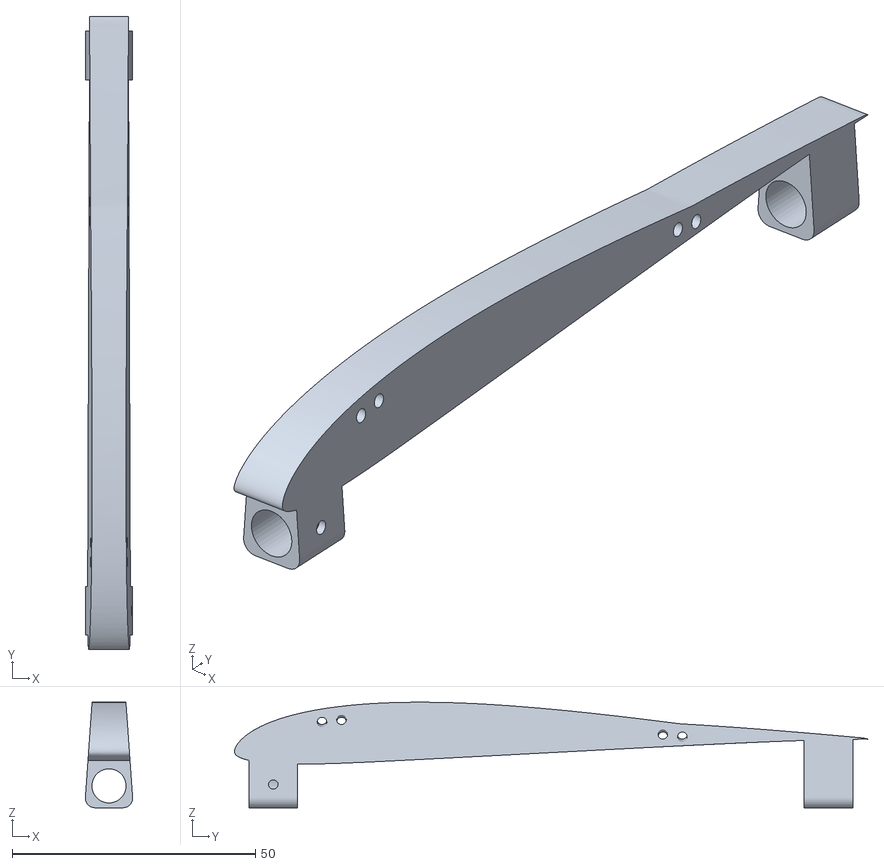
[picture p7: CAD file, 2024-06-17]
3D Files/stls 6:15:24/StratoSoar Rev2 v27_StratoSoar Rev2 v27_Wing mount_1_Body1.stl
9.70 x 130.0 x 21.7

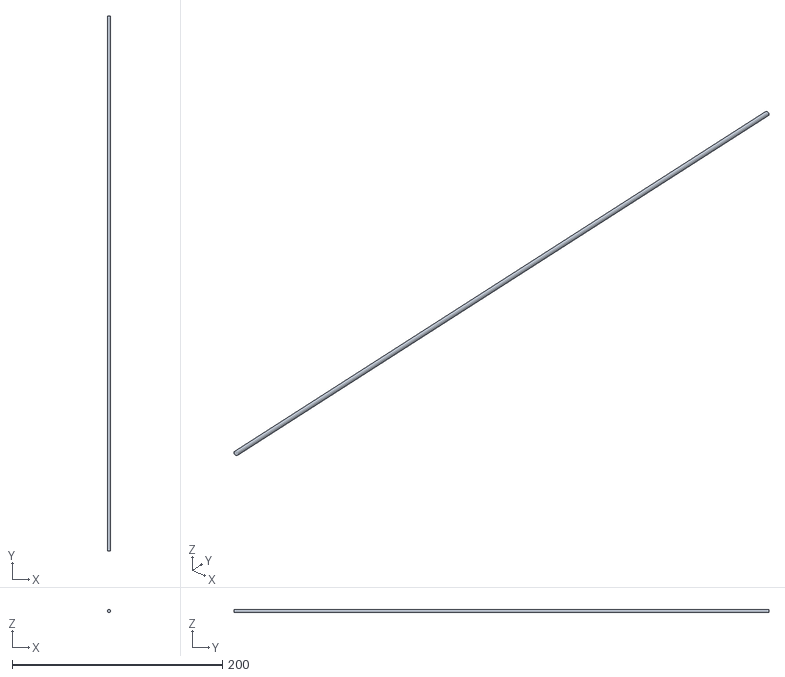
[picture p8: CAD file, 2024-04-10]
3D Files/StratoSoar design files/StratoSoar Rev2-stl.stl
3.00 x 509.0 x 3.00

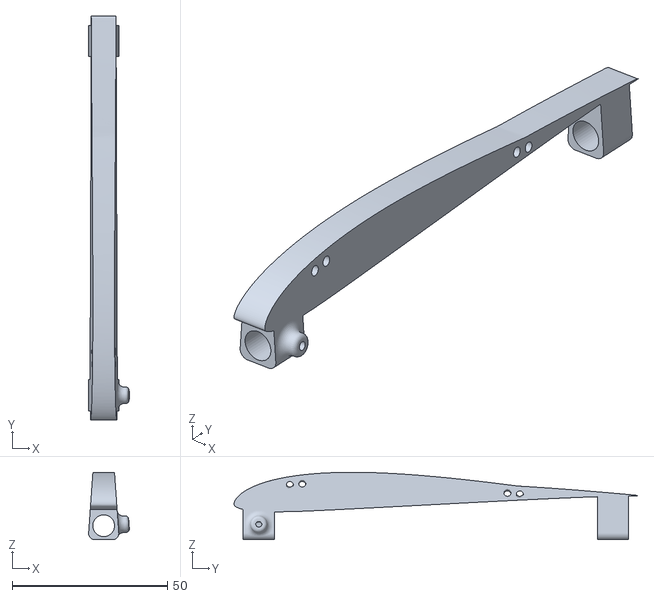
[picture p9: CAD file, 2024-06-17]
3D Files/StratoSoar Rev2 v35/StratoSoar Rev2 v35_StratoSoar Rev2 v35_Wing mount_1_Body1.stl
13.1 x 130.0 x 21.7

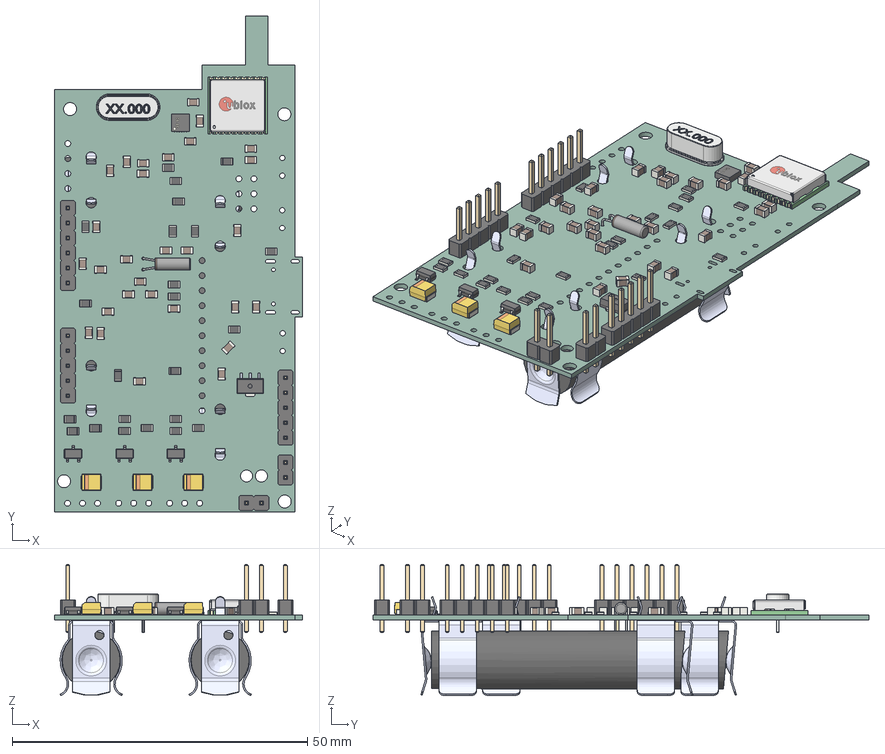
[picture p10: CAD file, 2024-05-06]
PCB + Schematic/StratoSoar-MK2.2/StratoSoar MK2.2.step
42.0 x 83.9 x 22.2 mm
R_0805_2012Metric x 23
CQ assembly
C_0805_2012Metric x 29
PinHeader_1x02_P254mm_Vertical x 2
PinHeader_1x05_P254mm_Vertical x 2
C26_LF_Horizontal
PinHeader_1x06_P254mm_Vertical
4C456F65-3891-4902-BF36-3E2D460C14F8
SC_59 x 3
CP_EIA_3528_21_Kemet_B x 3
F343147A-452A-42D3-8A28-AB9CB7AAC813
4BD6B2E8-BB7B-4AAE-9AFF-AA098B308A64
BK-82--3DModel-STEP-231308 v2 x 2
StratoSoar-MK2.2_PCB

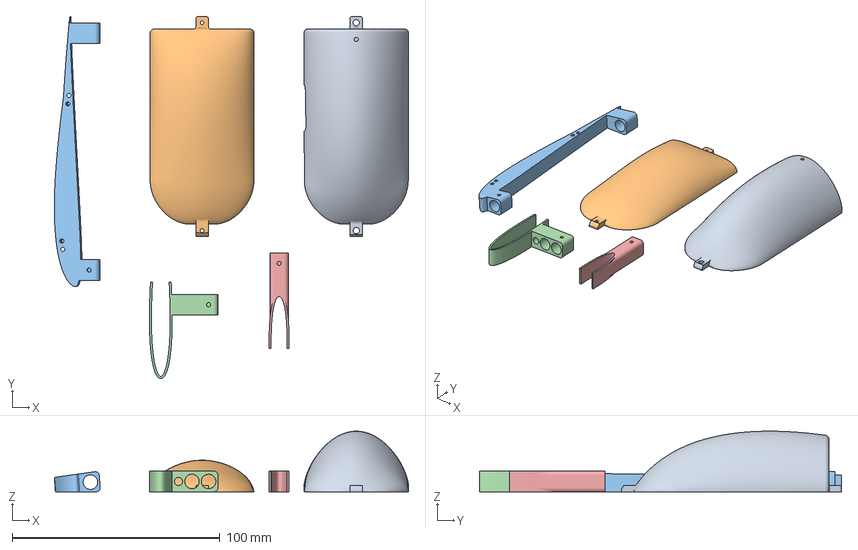
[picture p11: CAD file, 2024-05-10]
3D Files/objs 5:10:24/StratoSoar Rev2 v26_StratoSoar Rev2 v26_Wing mount_1_Body1.3mf
170.5 x 174.2 x 29.2 mm
StratoSoar Rev2 v26_StratoSoar Rev2 v26_Cockpit_1_Top half.obj
StratoSoar Rev2 v26_StratoSoar Rev2 v26_Cockpit_1_Bottom half.obj
StratoSoar Rev2 v26_StratoSoar Rev2 v26_Wing mount_1_Body1.obj
StratoSoar Rev2 v26_StratoSoar Rev2 v26_Horizontal mount_1_Horizontal mount.obj
StratoSoar Rev2 v26_StratoSoar Rev2 v26_Vertical mount_1_Body1.obj

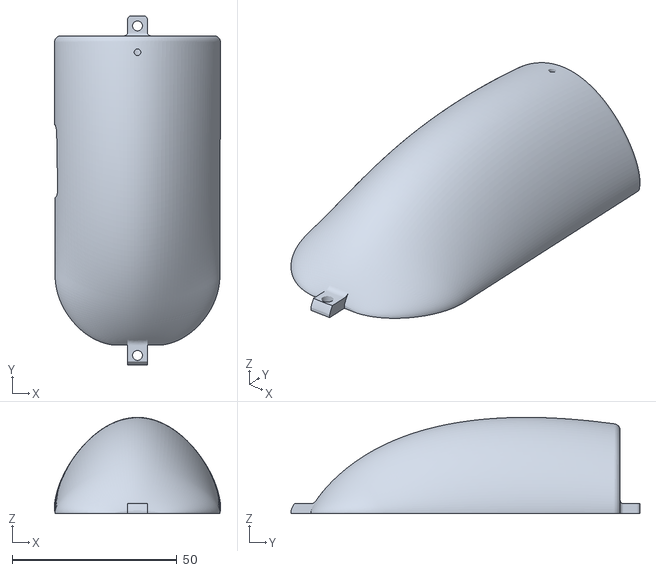
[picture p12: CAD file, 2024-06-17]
3D Files/stls 6:15:24/StratoSoar Rev2 v27_StratoSoar Rev2 v27_Cockpit_1_Top half.stl
50.4 x 105.9 x 29.2

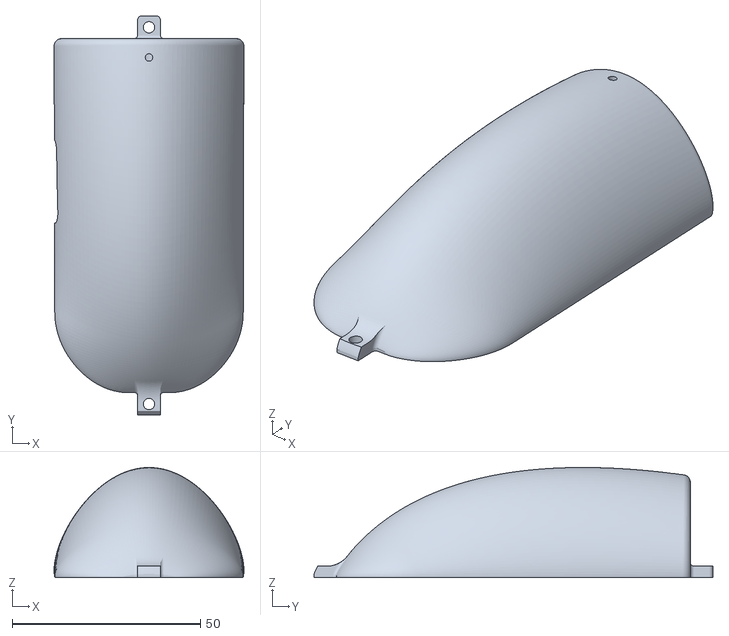
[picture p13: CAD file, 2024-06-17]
3D Files/StratoSoar Rev2 v28/StratoSoar Rev2 v28_StratoSoar Rev2 v27_Cockpit_1_Top half.stl
50.4 x 105.9 x 29.2

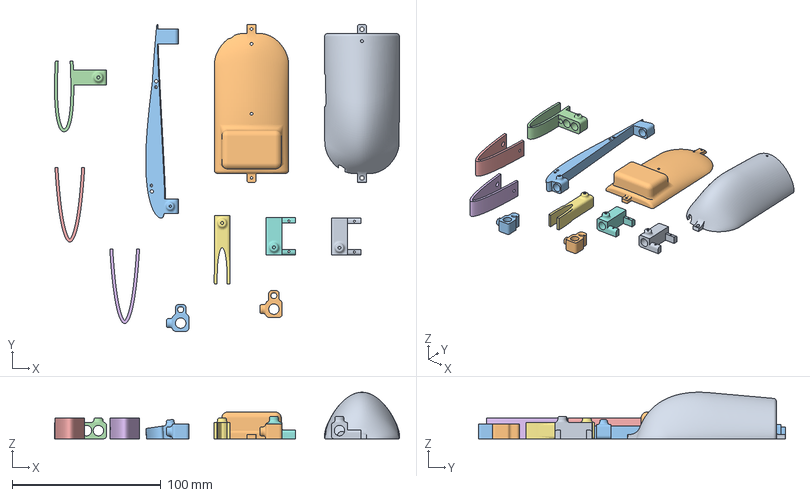
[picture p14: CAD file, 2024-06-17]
3D Files/StratoSoar Rev2 v35/StratoSoar Rev2 v35.3mf
231.8 x 206.0 x 31.3 mm
StratoSoar Rev2 v35_StratoSoar Rev2 v35_Cockpit_1_Top half.stl
StratoSoar Rev2 v35_StratoSoar Rev2 v35_Cockpit_1_Bottom half.stl
StratoSoar Rev2 v35_StratoSoar Rev2 v35_Wing mount_1_Body1.stl
StratoSoar Rev2 v35_StratoSoar Rev2 v35_Horizontal mount_1_Horizontal mount.stl
StratoSoar Rev2 v35_StratoSoar Rev2 v35_Bumper_1_Body1.stl x 2
StratoSoar Rev2 v35_StratoSoar Rev2 v35_Vertical mount_1_Body1.stl
StratoSoar Rev2 v35_StratoSoar Rev2 v35_Servo mount_1_Body1.stl x 2
StratoSoar Rev2 v35_StratoSoar Rev2 v35_Pushrod clip_2_Body1.stl x 2

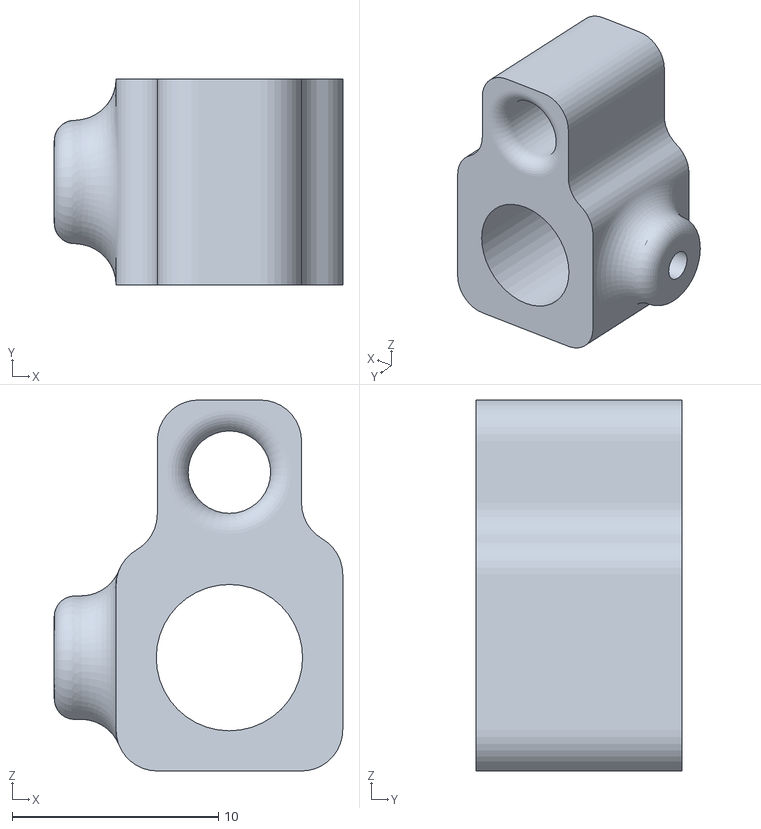
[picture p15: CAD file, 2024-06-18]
3D Files/StratoSoar Rev2 v36/StratoSoar Rev2 v36_StratoSoar Rev2 v36_Pushrod clip_1_Body1.stl
14.0 x 10.0 x 18.0

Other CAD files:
3D Files/StratoSoar Rev2 v36/StratoSoar Rev2 v36_StratoSoar Rev2 v36_Wing mount_1_Body1.stl
3D Files/StratoSoar design files/StratoSoar Rev2-step.stp
3D Files/StratoSoar Rev2 v27.3mf
3D Files/objs 5:10:24/StratoSoar Rev2 v26_StratoSoar Rev2 v26_Cockpit_1_Bottom half.obj
3D Files/stls 6:15:24/StratoSoar Rev2 v27_StratoSoar Rev2 v27_Cockpit_1_Bottom half.stl
3D Files/StratoSoar Rev2 v26.3mf
3D Files/Old formats/StratoSoar Rev2 v27.3mf
3D Files/Old formats/objs 5:10:24/StratoSoar Rev2 v26.3mf
3D Files/Old formats/objs 5:10:24/StratoSoar Rev2 v26_StratoSoar Rev2 v26_Cockpit_1_Bottom half.obj
3D Files/Old formats/objs 5:10:24/StratoSoar Rev2 v26_StratoSoar Rev2 v26_Horizontal mount_1_Horizontal mount.obj
3D Files/Old formats/objs 5:10:24/StratoSoar Rev2 v26_StratoSoar Rev2 v26_Vertical mount_1_Body1.obj
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

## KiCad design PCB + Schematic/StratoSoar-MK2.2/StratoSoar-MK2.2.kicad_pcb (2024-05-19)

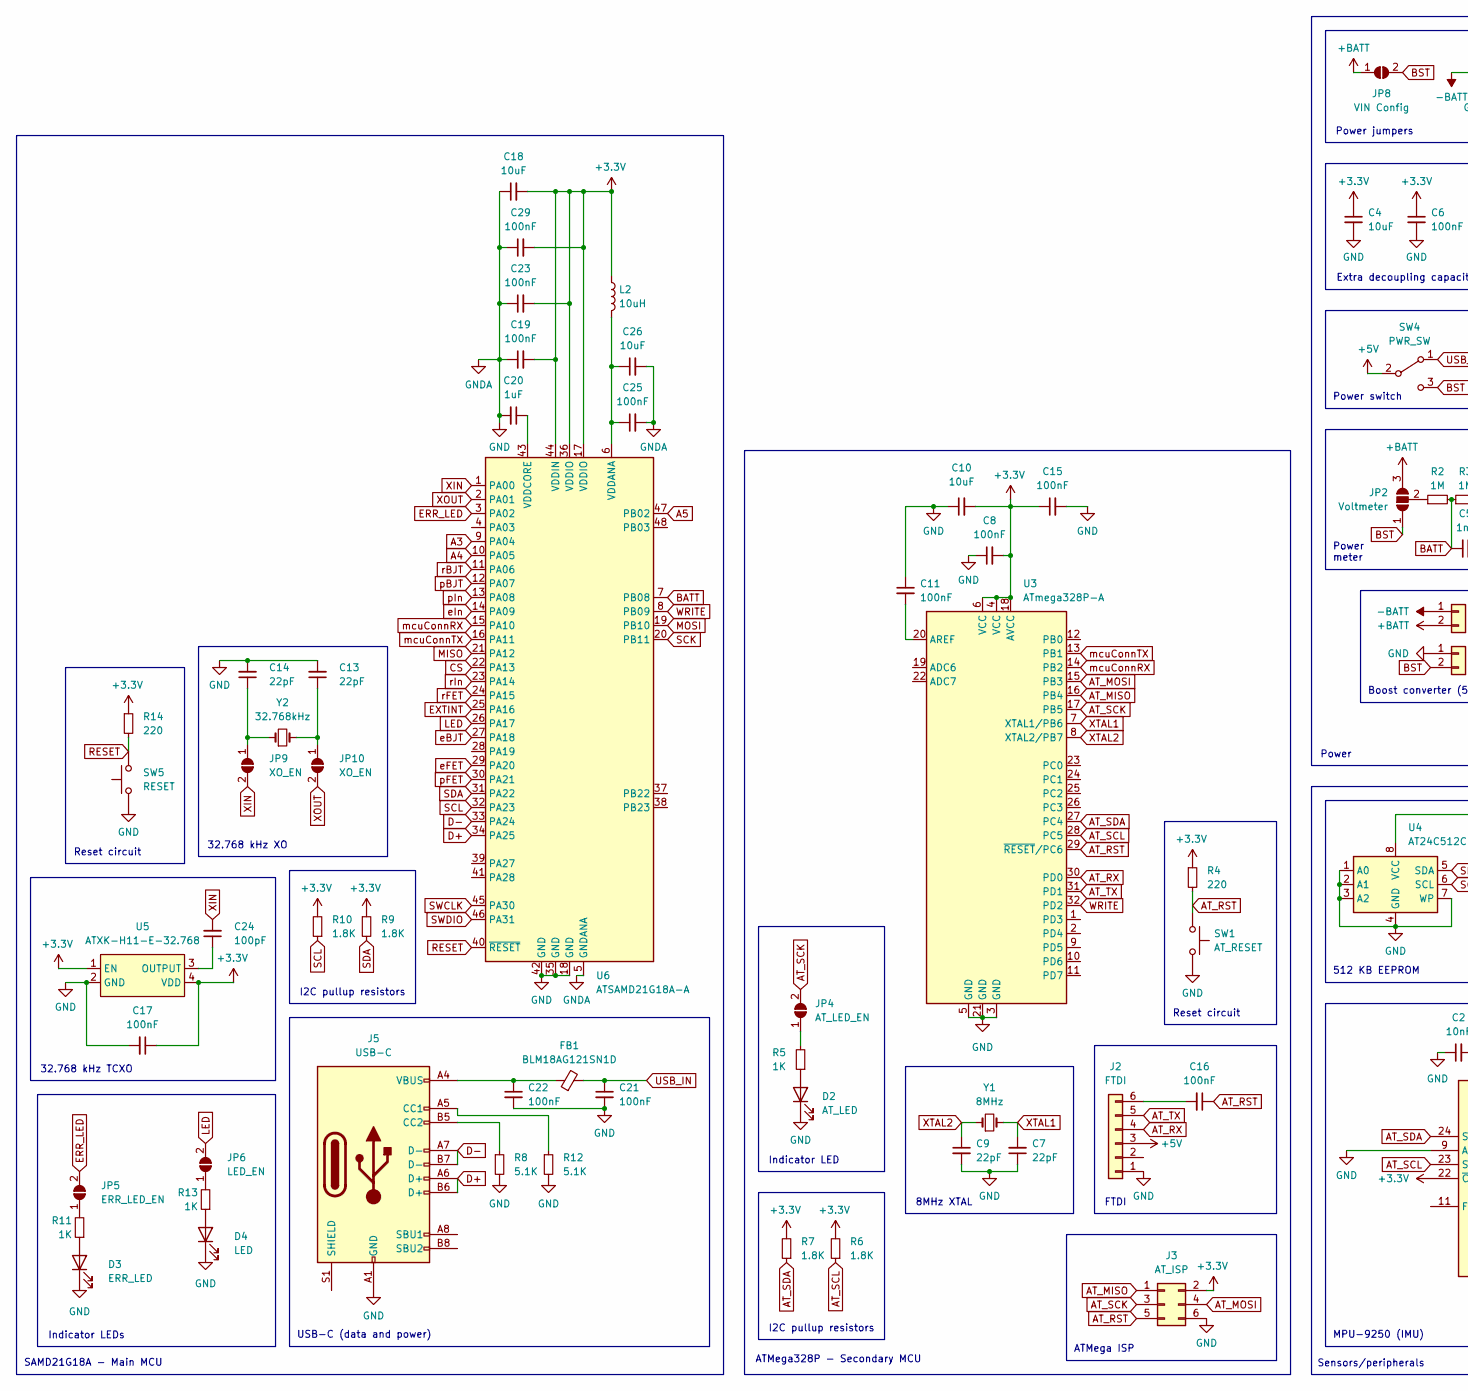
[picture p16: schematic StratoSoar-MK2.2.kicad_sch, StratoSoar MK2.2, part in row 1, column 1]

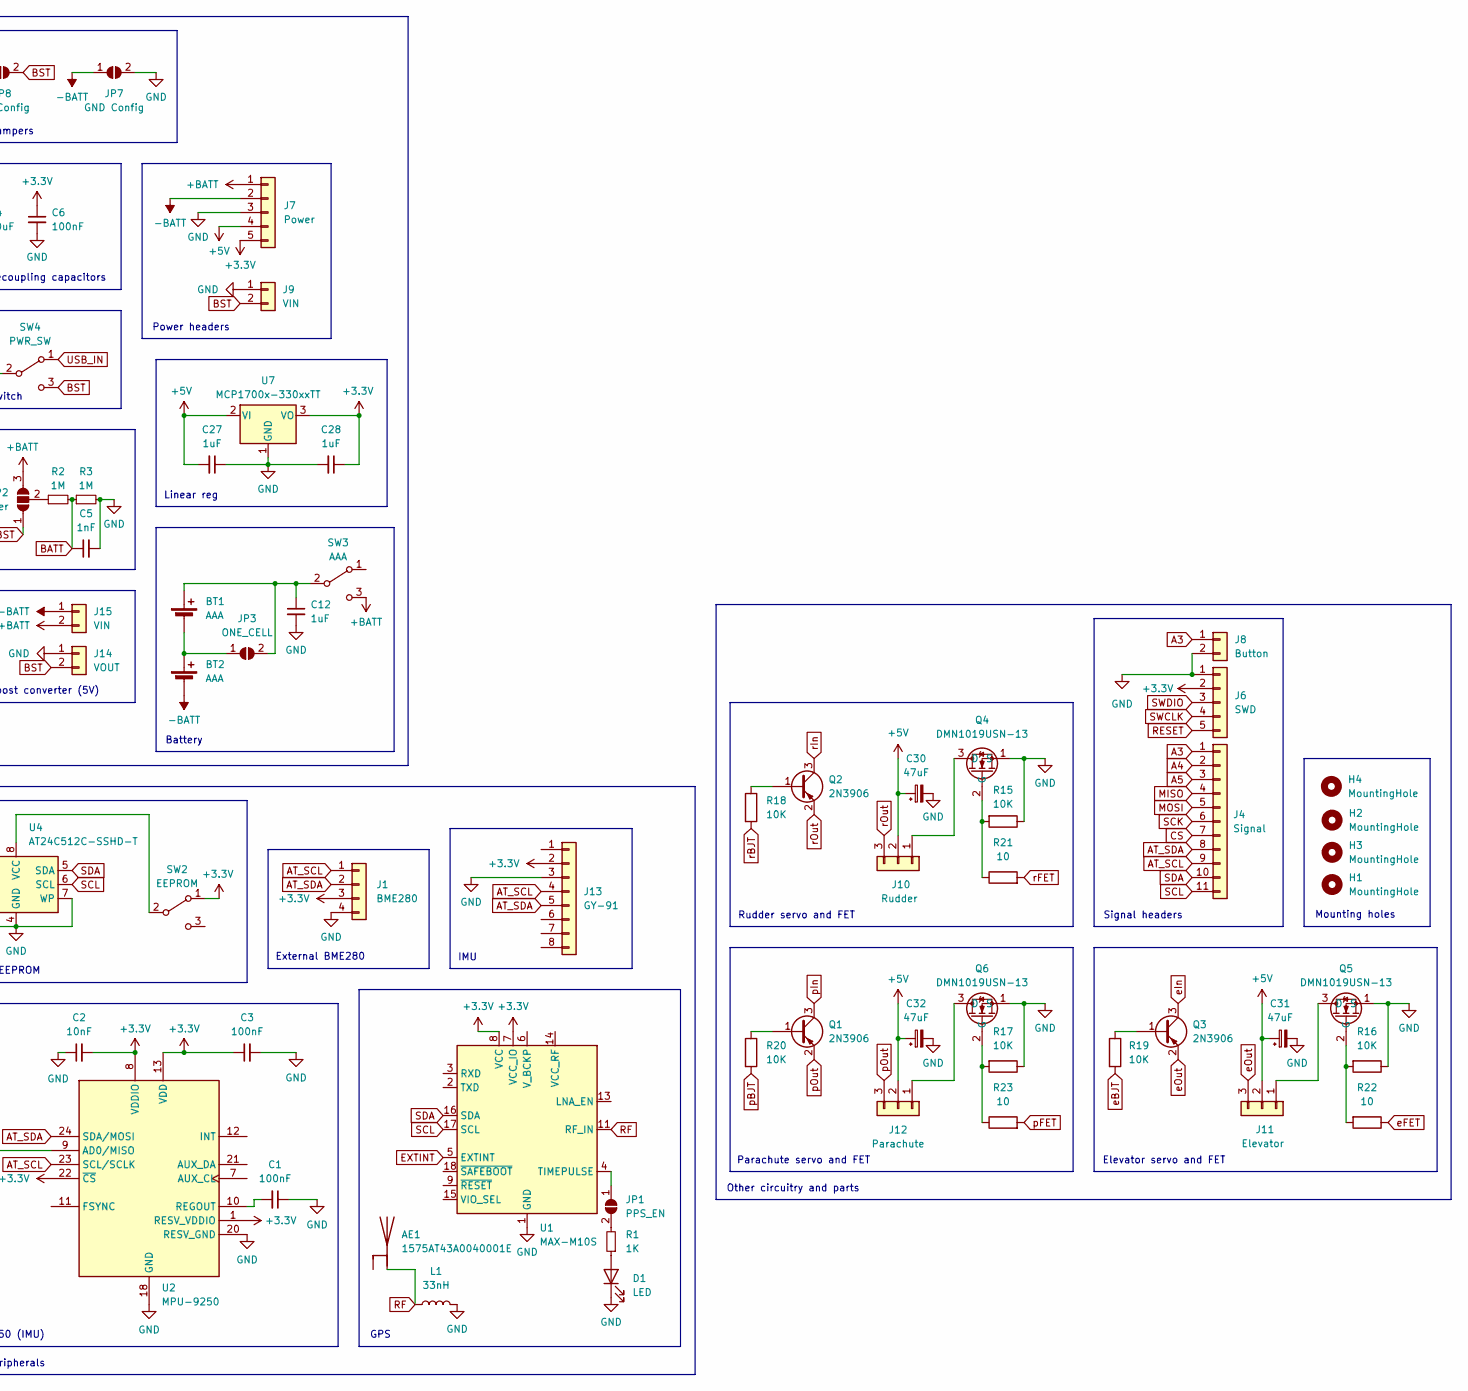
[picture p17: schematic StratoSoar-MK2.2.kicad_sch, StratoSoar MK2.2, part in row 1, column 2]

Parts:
AE1: 1575AT43A0040001E; ANT_1575AT_JOT-L
BT1, BT2: AAA; BatteryHolder_BK-82
C1, C3, C6, C8, C11, C15, C16, C17, C19, C21, C22, C23, C25, C29: 100nF; C_0805_2012Metric_Pad1.18x1.45mm_HandSolder
C2: 10nF; C_0805_2012Metric_Pad1.18x1.45mm_HandSolder
C4, C10, C18, C26: 10uF; C_0805_2012Metric_Pad1.18x1.45mm_HandSolder
C5: 1nF; C_0805_2012Metric_Pad1.18x1.45mm_HandSolder
C7, C9, C13, C14: 22pF; C_0805_2012Metric_Pad1.18x1.45mm_HandSolder
C12, C20, C27, C28: 1uF; C_0805_2012Metric_Pad1.18x1.45mm_HandSolder
C24: 100pF; C_0805_2012Metric_Pad1.18x1.45mm_HandSolder
C30, C31, C32: 47uF; CP_EIA-3528-21_Kemet-B
D1, D4: LED; LED_0805_2012Metric_Pad1.15x1.40mm_HandSolder
D2: AT_LED; LED_0805_2012Metric_Pad1.15x1.40mm_HandSolder
D3: ERR_LED; LED_0805_2012Metric_Pad1.15x1.40mm_HandSolder
FB1: BLM18AG121SN1D; R_0603_1608Metric_Pad0.98x0.95mm_HandSolder
H1, H2, H3, H4: MountingHole; MountingHole_2.2mm_M2
J1: BME280; PinHeader_1x04_P2.54mm_Vertical
J2: FTDI; PinHeader_1x06_P2.54mm_Vertical
J3: AT_ISP; PinHeader_2x03_P2.54mm_Vertical
J4: Signal; PinHeader_1x11_P2.54mm_Vertical
J5: USB-C; USB_C_Receptacle_GCT_USB4105-xx-A_16P_TopMnt_Horizontal
J6: SWD; PinHeader_1x05_P2.54mm_Vertical
J7: Power; PinHeader_1x05_P2.54mm_Vertical
J8: Button; PinHeader_1x02_P2.54mm_Vertical
J9: VIN; PinHeader_1x02_P2.54mm_Vertical
J10: Rudder; PinHeader_1x03_P2.54mm_Vertical
J11: Elevator; PinHeader_1x03_P2.54mm_Vertical
J12: Parachute; PinHeader_1x03_P2.54mm_Vertical
J13: GY-91; 1x08_SMD_Pads
J14: VOUT; 1x02_SMD_Pads
J15: VIN; 1x02_SMD_Pads
JP1: PPS_EN; SolderJumper-2_P1.3mm_Open_RoundedPad1.0x1.5mm
JP2: Voltmeter; SolderJumper-3_P1.3mm_Open_RoundedPad1.0x1.5mm_NumberLabels
JP3: ONE_CELL; SolderJumper-2_P1.3mm_Open_RoundedPad1.0x1.5mm
JP4: AT_LED_EN; SolderJumper-2_P1.3mm_Open_RoundedPad1.0x1.5mm
JP5: ERR_LED_EN; SolderJumper-2_P1.3mm_Open_RoundedPad1.0x1.5mm
JP6: LED_EN; SolderJumper-2_P1.3mm_Open_RoundedPad1.0x1.5mm
JP7: GND Config; SolderJumper-2_P1.3mm_Open_RoundedPad1.0x1.5mm
JP8: VIN Config; SolderJumper-2_P1.3mm_Open_RoundedPad1.0x1.5mm
JP9, JP10: XO_EN; SolderJumper-2_P1.3mm_Open_RoundedPad1.0x1.5mm
L1: 33nH; L_0805_2012Metric_Pad1.15x1.40mm_HandSolder
L2: 10uH; L_0805_2012Metric_Pad1.15x1.40mm_HandSolder
Q1, Q2, Q3: 2N3906; SOT-23-3
Q4, Q5, Q6: DMN1019USN-13; SC-59_Handsoldering
R1, R5, R11, R13: 1K; R_0805_2012Metric_Pad1.20x1.40mm_HandSolder
R2, R3: 1M; R_0805_2012Metric_Pad1.20x1.40mm_HandSolder
R4, R14: 220; R_0805_2012Metric_Pad1.20x1.40mm_HandSolder
R6, R7, R9, R10: 1.8K; R_0805_2012Metric_Pad1.20x1.40mm_HandSolder
R8, R12: 5.1K; R_0805_2012Metric_Pad1.20x1.40mm_HandSolder
R15, R16, R17, R18, R19, R20: 10K; R_0805_2012Metric_Pad1.20x1.40mm_HandSolder
R21, R22, R23: 10; R_0805_2012Metric_Pad1.20x1.40mm_HandSolder
SW1: AT_RESET; SW_SPST_CK_RS282G05A3
SW2: EEPROM; SW_SPDT_PCM12
SW3: AAA; SW_SPDT_PCM12
SW4: PWR_SW; SW_SPDT_PCM12
SW5: RESET; SW_SPST_CK_RS282G05A3
U1: MAX-M10S; ublox_MAX
U2: MPU-9250; InvenSense_QFN-24_3x3mm_P0.4mm
U3: ATmega328P-A; TQFP-32_7x7mm_P0.8mm
U4: AT24C512C-SSHD-T; SOIC-8_3.9x4.9mm_P1.27mm
U5: ATXK-H11-E-32.768; Crystal_SMD_Abracon_ABM8AIG-4Pin_3.2x2.5mm
U6: ATSAMD21G18A-A; TQFP-48_7x7mm_P0.5mm
U7: MCP1700x-330xxTT; SOT-89-3
Y1: 8MHz; Crystal_HC18-U_Vertical
Y2: 32.768kHz; Crystal_C26-LF_D2.1mm_L6.5mm_Horizontal

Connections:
+3.3V: C2.2, C3.1, C4.1, C6.1, C8.2, C10.2, C15.1, C17.1, C18.2, C19.2, C23.2, C28.1, C29.2, J1.3, J3.2, J6.2, J7.5, J13.2, L2.1, R4.1, R6.2, R7.2, R9.1, R10.2, R14.1, SW2.1 (A), U1.7 (VCC_IO), U1.8 (VCC), U2.1 (RESV_VDDIO), U2.8 (VDDIO), U2.13 (VDD), U2.22 (~CS), U3.4 (VCC), U3.6 (VCC), U3.18 (AVCC), U5.1 (EN), U5.4 (VDD), U6.17 (VDDIO), U6.36 (VDDIO), U6.44 (VDDIN), U7.3 (VO)
+5V: C27.2, C30.1, C31.1, C32.1, J2.3, J7.4, J10.2, J11.2, J12.2, SW4.2 (B), U7.2 (VI)
+BATT: J7.1, J15.2, JP2.3 (B), JP8.1 (A), SW3.3 (C)
-BATT: BT2.2 (-), J7.2, J15.1, JP7.1 (A)
A3: J4.1, J8.1, U6.9 (PA04)
A4: J4.2, U6.10 (PA05)
A5: J4.3, U6.47 (PB02)
AT_MISO: J3.1, U3.16 (PB4)
AT_MOSI: J3.4, U3.15 (PB3)
AT_RST: C16.1, J3.5, R4.2, SW1.1, U3.29 (~RESET/PC6)
AT_RX: J2.4, U3.30 (PD0)
AT_SCK: J3.3, JP4.2 (B), U3.17 (PB5)
AT_SCL: J1.1, J4.9, J13.4, R6.1, U2.23 (SCL/SCLK), U3.28 (PC5)
AT_SDA: J1.2, J4.8, J13.5, R7.1, U2.24 (SDA/MOSI), U3.27 (PC4)
AT_TX: J2.5, U3.31 (PD1)
BATT: C5.1, R2.2, R3.1, U6.7 (PB08)
BST: J9.2, J14.2, JP2.1 (A), JP8.2 (B), SW4.3 (C)
CS: J4.7, U6.22 (PA13)
D+: J5.A6 (D+), J5.B6 (D+), U6.34 (PA25)
D-: J5.A7 (D-), J5.B7 (D-), U6.33 (PA24)
ERR_LED: JP5.2 (B), U6.3 (PA02)
EXTINT: U1.5 (EXTINT), U6.25 (PA16)
GND: C1.1, C2.1, C3.2, C4.2, C5.2, C6.2, C7.1, C8.1, C9.2, C10.1, C11.1, C12.2, C13.2, C14.2, C15.2, C17.2, C18.1, C19.1, C20.2, C21.2, C22.2, C23.1, C25.2, C26.2, C27.1, C28.2, C29.1, C30.2, C31.2, C32.2, D1.1 (K), D2.1 (K), D3.1 (K), D4.1 (K), J1.4, J2.1, J3.6, J5.A1 (GND), J5.A12 (GND), J5.B1 (GND), J5.B12 (GND), J6.1, J7.3, J8.2, J9.1, J13.3, J14.1, JP7.2 (B), L1.2, Q4.1 (S), Q5.1 (S), Q6.1 (S), R3.2, R8.2, R12.2, R15.1, R16.1, R17.1, SW1.2, SW5.1, U1.1 (GND), U1.10 (GND), U1.12 (GND), U2.9 (AD0/MISO), U2.18 (GND), U2.20 (RESV_GND), U3.3 (GND), U3.5 (GND), U3.21 (GND), U4.1 (A0), U4.2 (A1), U4.3 (A2), U4.4 (GND), U4.7 (WP), U5.2 (GND), U6.5 (GNDANA), U6.18 (GND), U6.35 (GND), U6.42 (GND), U7.1 (GND)
LED: JP6.2 (B), U6.26 (PA17)
MISO: J4.4, U6.21 (PA12)
MOSI: J4.5, U6.19 (PB10)
unnamed: BT1.1 (+), C12.1, JP3.2 (B), SW3.2 (B)
unnamed: BT1.2 (-), BT2.1 (+), JP3.1 (A)
unnamed: C22.1, FB1.1, J5.A4 (VBUS), J5.A9 (VBUS), J5.B4 (VBUS), J5.B9 (VBUS)
unnamed: D1.2 (A), R1.1
unnamed: D2.2 (A), R5.1
unnamed: D3.2 (A), R11.1
unnamed: D4.2 (A), R13.1
unnamed: C16.2, J2.6
unnamed: J5.A5 (CC1), R12.1
unnamed: J5.B5 (CC2), R8.1
unnamed: J10.1, Q4.3 (D)
unnamed: J11.1, Q5.3 (D)
unnamed: J12.1, Q6.3 (D)
unnamed: JP1.1 (A), U1.4 (TIMEPULSE)
unnamed: JP1.2 (B), R1.2
unnamed: JP2.2 (C), R2.1
unnamed: JP4.1 (A), R5.2
unnamed: JP5.1 (A), R11.2
unnamed: JP6.1 (A), R13.2
unnamed: C14.1, JP9.1 (A), Y2.1
unnamed: C13.1, JP10.1 (A), Y2.2
unnamed: Q1.1 (B), R20.1
unnamed: Q2.1 (B), R18.1
unnamed: Q3.1 (B), R19.1
unnamed: Q4.2 (G), R15.2, R21.1
unnamed: Q5.2 (G), R16.2, R22.2
unnamed: Q6.2 (G), R17.2, R23.1
unnamed: SW2.2 (B), U4.8 (VCC)
unnamed: C1.2, U2.10 (REGOUT)
unnamed: C11.2, U3.20 (AREF)
unnamed: C24.1, U5.3 (OUTPUT)
unnamed: C25.1, C26.1, L2.2, U6.6 (VDDANA)
unnamed: C20.1, U6.43 (VDDCORE)
RESET: J6.5, R14.2, SW5.2, U6.40 (~RESET)
RF: AE1.1 (FEED), L1.1, U1.11 (RF_IN)
SCK: J4.6, U6.20 (PB11)
SCL: J4.11, R10.1, U1.17 (SCL), U4.6 (SCL), U6.32 (PA23)
SDA: J4.10, R9.2, U1.16 (SDA), U4.5 (SDA), U6.31 (PA22)
SWCLK: J6.4, U6.45 (PA30)
SWDIO: J6.3, U6.46 (PA31)
USB_IN: C21.1, FB1.2, SW4.1 (A)
WRITE: U3.32 (PD2), U6.8 (PB09)
XIN: C24.2, JP9.2 (B), U6.1 (PA00)
XOUT: JP10.2 (B), U6.2 (PA01)
XTAL1: C7.2, U3.7 (XTAL1/PB6), Y1.2
XTAL2: C9.1, U3.8 (XTAL2/PB7), Y1.1
eBJT: R19.2, U6.27 (PA18)
eFET: R22.1, U6.29 (PA20)
eIn: Q3.3 (C), U6.14 (PA09)
eOut: J11.3, Q3.2 (E)
mcuConnRX: U3.14 (PB2), U6.15 (PA10)
mcuConnTX: U3.13 (PB1), U6.16 (PA11)
pBJT: R20.2, U6.12 (PA07)
pFET: R23.2, U6.30 (PA21)
pIn: Q1.3 (C), U6.13 (PA08)
pOut: J12.3, Q1.2 (E)
rBJT: R18.2, U6.11 (PA06)
rFET: R21.2, U6.24 (PA15)
rIn: Q2.3 (C), U6.23 (PA14)
rOut: J10.3, Q2.2 (E)

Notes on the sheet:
Battery
Indicator LEDs
IMU
ATMega328P - Secondary MCU
Other circuitry and parts
Power jumpers
8MHz XTAL
I2C pullup resistors
External BME280
FTDI
Power meter
Elevator servo and FET
ATMega ISP
Linear reg
Power
Power headers
Mounting holes
Reset circuit
Parachute servo and FET
SAMD21G18A - Main MCU
Boost converter (5V)
USB-C (data and power)
32.768 kHz TCXO
MPU-9250 (IMU)
32.768 kHz XO
Sensors/peripherals
Extra decoupling capacitors
GPS
512 KB EEPROM
Rudder servo and FET
Power switch
Signal headers
Indicator LED

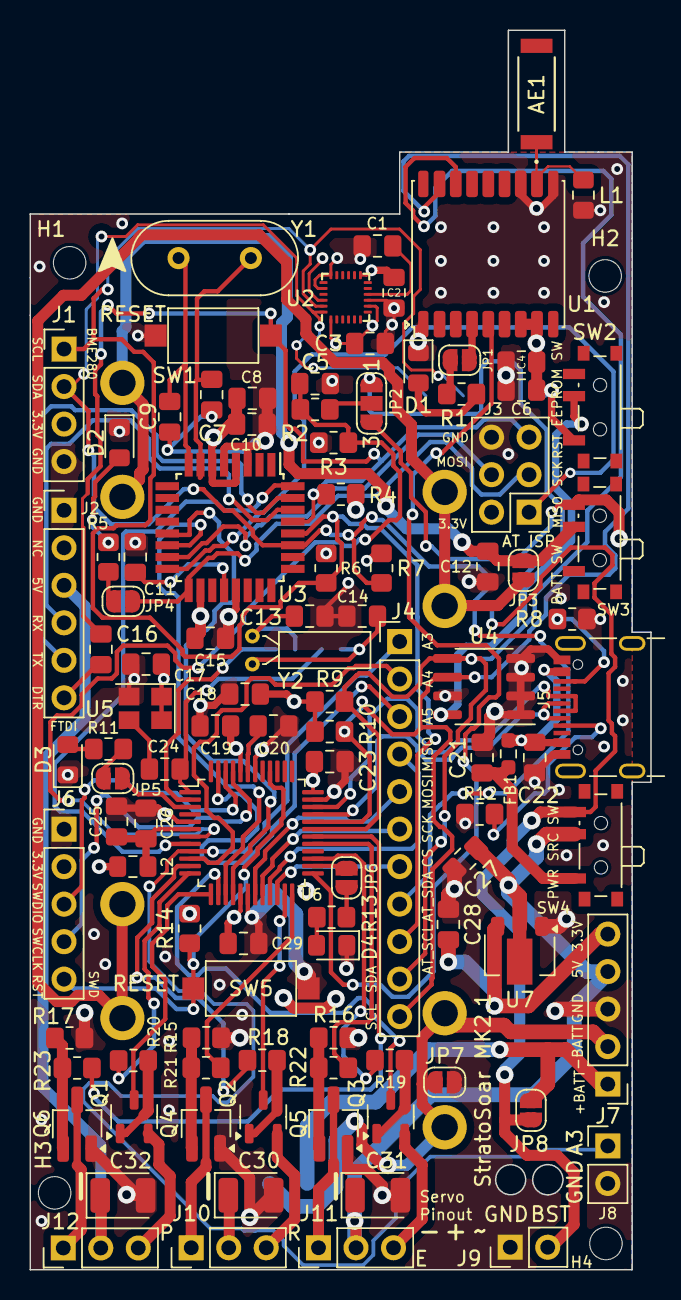
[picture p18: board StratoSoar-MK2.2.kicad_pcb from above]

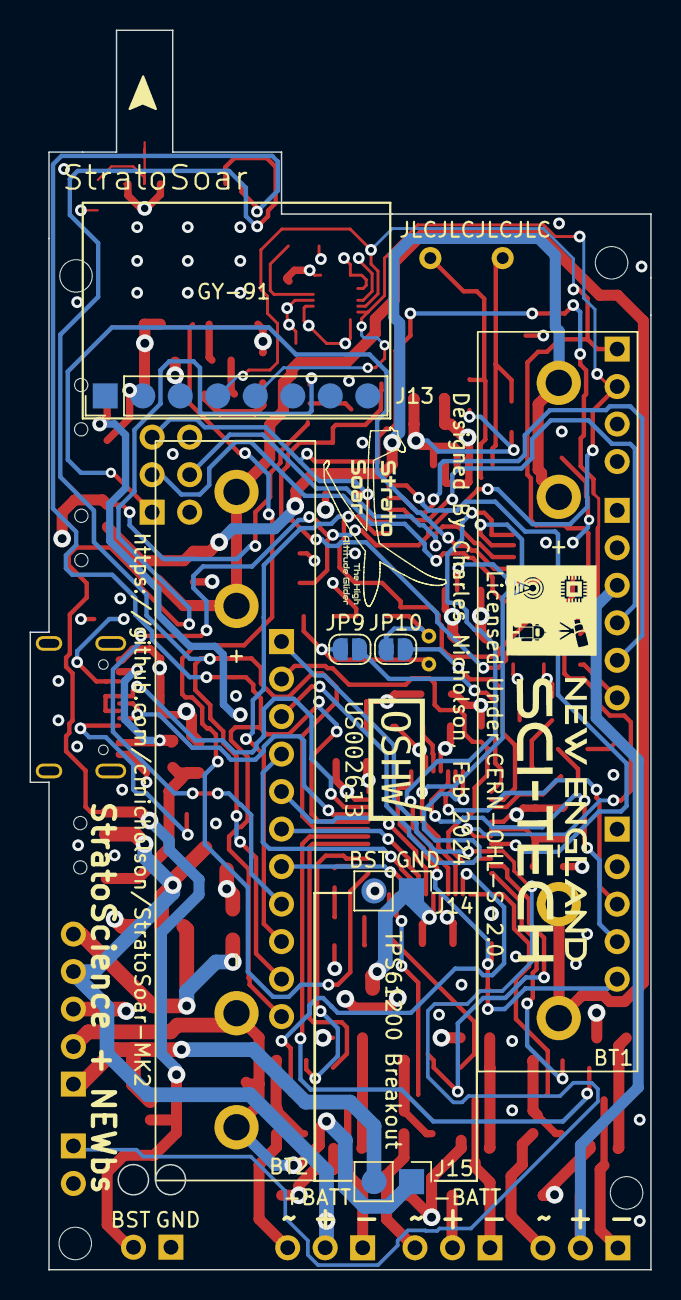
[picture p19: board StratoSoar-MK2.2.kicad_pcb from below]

Board: 4 copper layers, 42.0 x 83.9 mm, 114 parts (7 on the bottom side), 86 nets.

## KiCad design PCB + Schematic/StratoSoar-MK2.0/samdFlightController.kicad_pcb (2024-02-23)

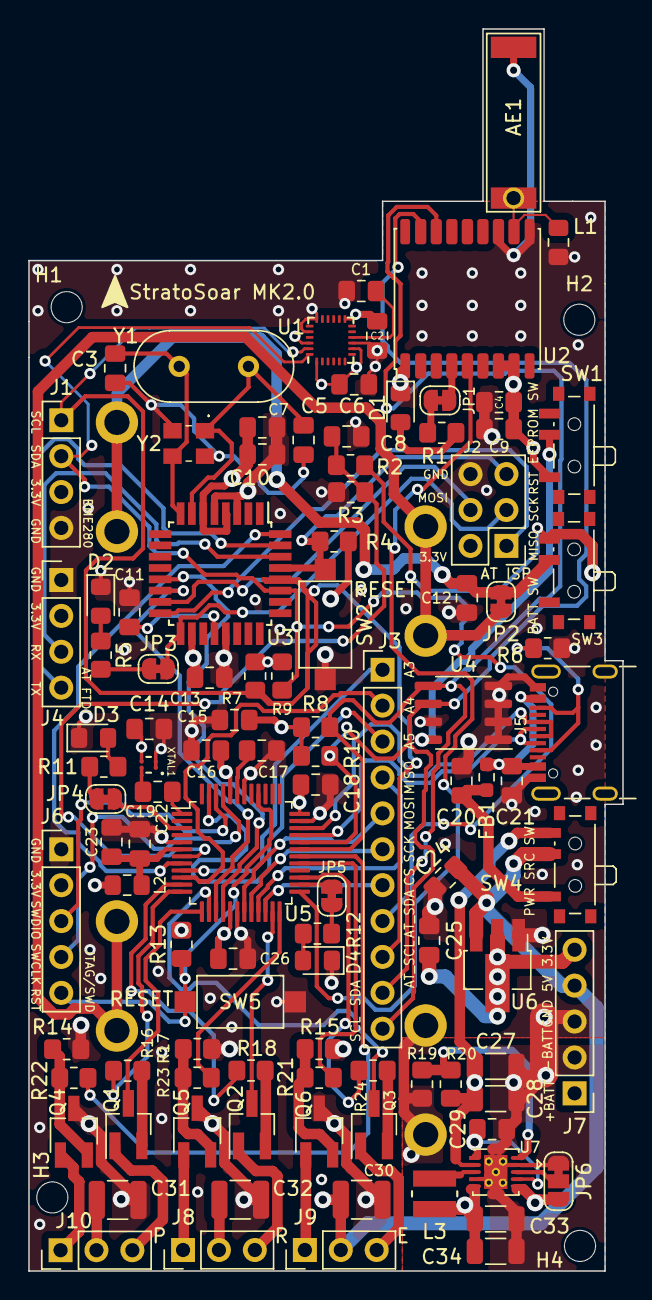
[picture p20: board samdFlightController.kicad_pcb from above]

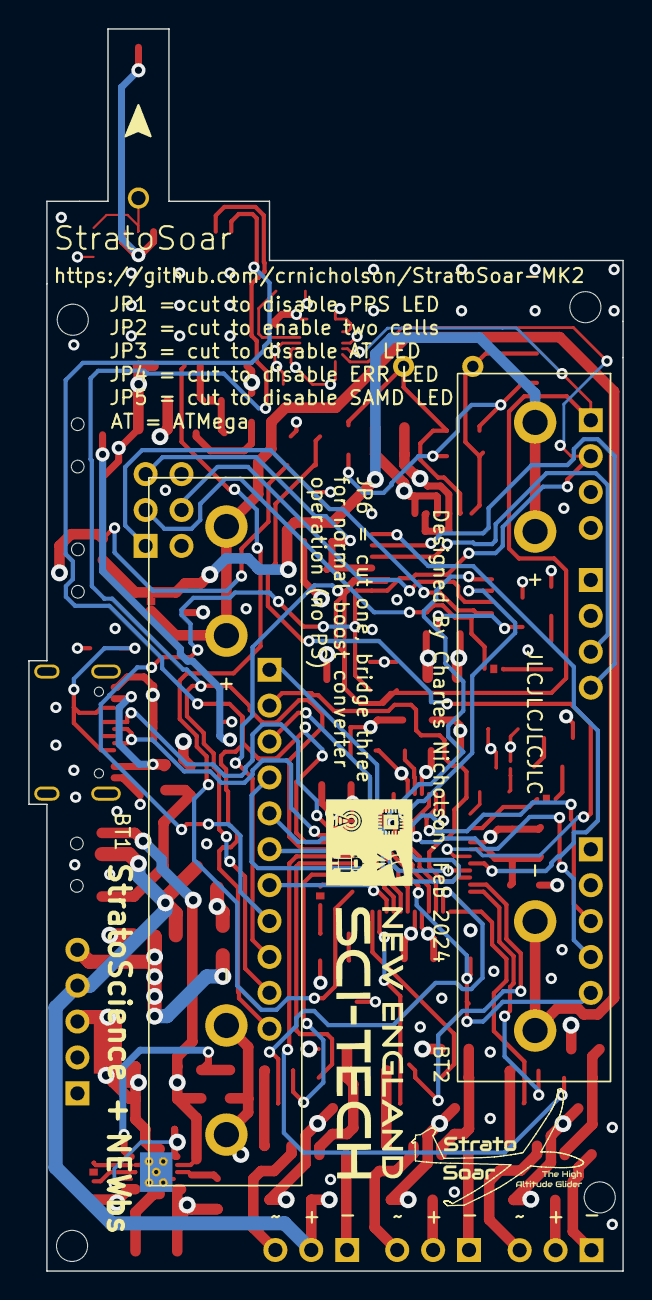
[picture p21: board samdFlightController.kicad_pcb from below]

Board: 4 copper layers, 42.0 x 87.9 mm, 111 parts (2 on the bottom side), 84 nets.

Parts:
AE1: Antenna_Chip; RAINSUN_GPS1003
BT1, BT2: AAA; BatteryHolder_BK-82
C1, C7, C9, C11, C13, C16, C18, C23, C26: 100nF; C_0805_2012Metric_Pad1.18x1.45mm_HandSolder
C2: 10 nF (U2); C_0805_2012Metric_Pad1.18x1.45mm_HandSolder
C3, C5: 22pF; C_0805_2012Metric_Pad1.18x1.45mm_HandSolder
C4, C10, C15, C22: 10uF; C_0805_2012Metric_Pad1.18x1.45mm_HandSolder
C6: 100 nF (U2); C_0805_2012Metric_Pad1.18x1.45mm_HandSolder
C8: 1nF; C_0805_2012Metric_Pad1.18x1.45mm_HandSolder
C12: 1 uF (BT1); C_0805_2012Metric_Pad1.18x1.45mm_HandSolder
C14: 100 nF (XTAL1); C_0805_2012Metric_Pad1.18x1.45mm_HandSolder
C17: 1uF; C_0805_2012Metric_Pad1.18x1.45mm_HandSolder
C19: 100 pF (XTAL1); C_0805_2012Metric_Pad1.18x1.45mm_HandSolder
C20, C21: 100 nF (J1); C_0805_2012Metric_Pad1.18x1.45mm_HandSolder
C24, C25: 1 uF (U1); C_0805_2012Metric_Pad1.18x1.45mm_HandSolder
C27, C33: 100nF (U7); C_1206_3216Metric
C28: 22uF (U7); C_1206_3216Metric
C29: 100nF (U7); C_0805_2012Metric_Pad1.18x1.45mm_HandSolder
C30: 47uF (J10); C_1210_3225Metric
C31: 47uF (J7); C_1210_3225Metric
C32: 47uF (J9); C_1210_3225Metric
C34: 10uF (U7); C_1206_3216Metric
D1, D4: LED; LED_0805_2012Metric_Pad1.15x1.40mm_HandSolder
D2: AT_LED; LED_0805_2012Metric_Pad1.15x1.40mm_HandSolder
D3: ERR_LED; LED_0805_2012Metric_Pad1.15x1.40mm_HandSolder
FB1: BLM18AG121SN1D (J1); R_0603_1608Metric_Pad0.98x0.95mm_HandSolder
H1, H2, H3, H4: MountingHole; MountingHole_2.2mm_M2
J1: BME280; PinHeader_1x04_P2.54mm_Vertical
J2: AT_ISP; PinHeader_2x03_P2.54mm_Vertical
J3: Signal; PinHeader_1x11_P2.54mm_Vertical
J4: AT_FTDI; PinHeader_1x04_P2.54mm_Vertical
J5: USB_C_Receptacle_USB2.0; USB_C_Receptacle_GCT_USB4105-xx-A_16P_TopMnt_Horizontal
J6: JTAG; PinHeader_1x05_P2.54mm_Vertical
J7: Power; PinHeader_1x05_P2.54mm_Vertical
J8: rudder; PinHeader_1x03_P2.54mm_Vertical
J9: elevator; PinHeader_1x03_P2.54mm_Vertical
J10: parachute; PinHeader_1x03_P2.54mm_Vertical
JP1: PPS_EN; SolderJumper-2_P1.3mm_Bridged_RoundedPad1.0x1.5mm
JP2: ONE_CELL; SolderJumper-2_P1.3mm_Bridged_RoundedPad1.0x1.5mm
JP3: AT_LED_EN; SolderJumper-2_P1.3mm_Bridged_RoundedPad1.0x1.5mm
JP4: ERR_LED_EN; SolderJumper-2_P1.3mm_Bridged_RoundedPad1.0x1.5mm
JP5: LED_EN; SolderJumper-2_P1.3mm_Bridged_RoundedPad1.0x1.5mm
JP6: PS_EN; SolderJumper-3_P1.3mm_Bridged12_RoundedPad1.0x1.5mm
L1: 33nH; L_0805_2012Metric_Pad1.15x1.40mm_HandSolder
L2: 10uH; L_0805_2012Metric_Pad1.15x1.40mm_HandSolder
L3: LPS3015-222ML; IND_LPS3015
NT1: GND connection; NetTie-2_SMD_Pad2.0mm
Q1, Q2, Q3: 2N3906; SOT-23_Handsoldering
Q4, Q5, Q6: DMN1019USN-13; SC-59_Handsoldering
R1, R5, R11, R12: 1K; R_0805_2012Metric_Pad1.20x1.40mm_HandSolder
R2, R3: 1M; R_0805_2012Metric_Pad1.20x1.40mm_HandSolder
R4, R13, R15, R16, R17, R18, R22, R24: 10K; R_0805_2012Metric_Pad1.20x1.40mm_HandSolder
R6: 5.1 K (J1); R_0805_2012Metric_Pad1.20x1.40mm_HandSolder
R7, R8, R9, R10: 1.8K; R_0805_2012Metric_Pad1.20x1.40mm_HandSolder
R14, R21, R23: 10; R_0805_2012Metric_Pad1.20x1.40mm_HandSolder
R19: 91K; R_0805_2012Metric_Pad1.20x1.40mm_HandSolder
R20: 820K; R_0805_2012Metric_Pad1.20x1.40mm_HandSolder
SW1: EEPROM; SW_SPDT_PCM12
SW2: AT_RESET; SW_SPST_CK_RS282G05A3
SW3: AAA; SW_SPDT_PCM12
SW4: PWR_SW; SW_SPDT_PCM12
SW5: RESET; SW_SPST_CK_RS282G05A3
U1: MPU-9250; InvenSense_QFN-24_3x3mm_P0.4mm
U2: MAX-M10S; ublox_MAX
U3: ATmega328P-A; TQFP-32_7x7mm_P0.8mm
U4: AT24C512C-SSHD-T; SOIC-8_3.9x4.9mm_P1.27mm
U5: ATSAMD21G18A-A; TQFP-48_7x7mm_P0.5mm
U6: MCP1700x-330xxTT; SOT-89-3_Handsoldering
U7: TPS61200DRC; Texas_S-PVSON-N10_ThermalVias
XTAL1: SIT1552AI-JF-DCC-32.768D; BGA4_SiT1532_SIT
Y1: 8MHz; Crystal_HC18-U_Vertical
Y2: ECS-80-10; ECS801033CHNTR

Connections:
+3.3V: C2.2, C4.1, C6.1, C7.2, C9.1, C10.2, C13.1, C14.2, C15.2, C16.2, C18.2, C25.1, C26.2, J1.3, J2.2, J4.2, J6.2, J7.5, L2.1, R4.1, R7.2, R8.1, R9.2, R10.2, R13.1, SW1.1 (A), U1.1 (RESV_VDDIO), U1.8 (VDDIO), U1.13 (VDD), U1.22 (~CS), U2.7 (VCC_IO), U2.8 (VCC), U3.4 (VCC), U3.6 (VCC), U3.18 (AVCC), U5.17 (VDDIO), U5.36 (VDDIO), U5.44 (VDDIN), U6.2 (VO), XTAL1.3 (VDD)
+5V: C24.2, C30.1, C31.1, C32.1, J7.4, J8.2, J9.2, J10.2, SW4.2 (B), U6.3 (VI)
+BATT: C33.1, C34.1, J7.1, JP6.3 (B), L3.2, R2.1, SW3.3 (C), U7.5 (VIN), U7.6 (EN)
-BATT: BT1.2 (-), C27.2, C28.2, C29.2, C33.2, C34.2, J7.2, JP6.1 (A), NT1.1, R19.2, U7.4 (PGND), U7.9 (GND), U7.11 (PAD)
A3: J3.1, U5.9 (PA04)
A4: J3.2, U5.10 (PA05)
A5: J3.3, U5.47 (PB02)
AT_MISO: J2.1, U3.16 (PB4)
AT_MOSI: J2.4, U3.15 (PB3)
AT_RST: J2.5, R4.2, SW2.1, U3.29 (~RESET/PC6)
AT_RX: J4.3, U3.30 (PD0)
AT_SCK: J2.3, JP3.2 (B), U3.17 (PB5)
AT_SCL: J1.1, J3.9, R7.1, U1.23 (SCL/SCLK), U3.28 (PC5)
AT_SDA: J1.2, J3.8, R9.1, U1.24 (SDA/MOSI), U3.27 (PC4)
AT_TX: J4.4, U3.31 (PD1)
BATT: C8.1, R2.2, R3.1, U5.7 (PB08)
BST: C27.1, C28.1, R20.1, SW4.3 (C), U7.2 (VOUT)
CS: J3.7, U5.22 (PA13)
D+: J5.A6 (D+), J5.B6 (D+), U5.34 (PA25)
D-: J5.A7 (D-), J5.B7 (D-), U5.33 (PA24)
EXTINT: U2.5 (EXTINT), U5.25 (PA16)
GND: AE1.1 (GND), C1.1, C2.1, C3.2, C4.2, C5.2, C6.2, C7.1, C8.2, C9.2, C10.1, C11.1, C12.2, C13.2, C14.1, C15.1, C16.1, C17.2, C18.1, C20.2, C21.2, C22.2, C23.2, C24.1, C25.2, C26.1, C30.2, C31.2, C32.2, D1.1 (K), D2.1 (K), D3.1 (K), D4.1 (K), J1.4, J2.6, J4.1, J5.A1 (GND), J5.A12 (GND), J5.B1 (GND), J5.B12 (GND), J6.1, J7.3, L1.2, NT1.2, Q4.3 (S), Q5.3 (S), Q6.3 (S), R3.2, R6.2, R15.1, R17.1, R22.1, SW2.2, SW5.1, U1.9 (AD0/MISO), U1.18 (GND), U1.20 (RESV_GND), U2.1 (GND), U2.10 (GND), U2.12 (GND), U3.3 (GND), U3.5 (GND), U3.21 (GND), U4.1 (A0), U4.2 (A1), U4.3 (A2), U4.4 (GND), U4.7 (WP), U5.5 (GNDANA), U5.18 (GND), U5.35 (GND), U5.42 (GND), U6.1 (GND), XTAL1.1 (GND), XTAL1.4 (GND), Y2.2, Y2.4
MISO: J3.4, U5.21 (PA12)
MOSI: J3.5, U5.19 (PB10)
unnamed: BT2.1 (+), C12.1, JP2.2 (B), SW3.2 (B)
unnamed: BT1.1 (+), BT2.2 (-), JP2.1 (A)
unnamed: C21.1, FB1.1, J5.A4 (VBUS), J5.A9 (VBUS), J5.B4 (VBUS), J5.B9 (VBUS)
unnamed: D1.2 (A), R1.1
unnamed: D2.2 (A), R5.1
unnamed: D3.2 (A), R11.1
unnamed: D4.2 (A), R12.1
unnamed: J8.1, Q5.1 (D)
unnamed: J9.1, Q6.1 (D)
unnamed: J10.1, Q4.1 (D)
unnamed: J5.A5 (CC1), J5.B5 (CC2), R6.1
unnamed: JP1.1 (A), U2.4 (TIMEPULSE)
unnamed: JP1.2 (B), R1.2
unnamed: JP3.1 (A), R5.2
unnamed: JP4.1 (A), R11.2
unnamed: JP4.2 (B), U5.3 (PA02)
unnamed: JP5.1 (A), R12.2
unnamed: JP5.2 (B), U5.26 (PA17)
unnamed: JP6.2 (C), U7.8 (PS)
unnamed: Q1.2 (B), R16.1
unnamed: Q2.2 (B), R18.1
unnamed: Q3.2 (B), R24.1
unnamed: Q4.2 (G), R14.1, R22.2
unnamed: Q5.2 (G), R17.2, R23.1
unnamed: Q6.2 (G), R15.2, R21.2
unnamed: SW1.2 (B), U4.8 (VCC)
unnamed: C1.2, U1.10 (REGOUT)
unnamed: C11.2, U3.20 (AREF)
unnamed: C19.2, U5.1 (PA00)
unnamed: C22.1, C23.1, L2.2, U5.6 (VDDANA)
unnamed: C17.1, U5.43 (VDDCORE)
unnamed: R19.1, R20.2, U7.10 (FB)
unnamed: L3.1, U7.3 (L)
unnamed: C19.1, XTAL1.2 (CLK_OUT)
RESET: J6.5, R13.2, SW5.2, U5.40 (~RESET)
RF: AE1.2 (RF), L1.1, U2.11 (RF_IN)
SCK: J3.6, U5.20 (PB11)
SCL: J3.11, R10.1, U2.17 (SCL), U4.6 (SCL), U5.32 (PA23)
SDA: J3.10, R8.2, U2.16 (SDA), U4.5 (SDA), U5.31 (PA22)
SWCLK: J6.4, U5.45 (PA30)
SWDIO: J6.3, U5.46 (PA31)
USB_IN: C20.1, FB1.2, SW4.1 (A)
VAUX: C29.1, U7.1 (VAUX), U7.7 (UVLO)
WRITE: U3.32 (PD2), U5.8 (PB09)
XTAL1: C5.1, U3.7 (XTAL1/PB6), Y1.2, Y2.1
XTAL2: C3.1, U3.8 (XTAL2/PB7), Y1.1, Y2.3
eBJT: R24.2, U5.27 (PA18)
eFET: R21.1, U5.29 (PA20)
eIn: Q3.3 (C), U5.14 (PA09)
eOut: J9.3, Q3.1 (E)
mcuConnRX: U3.14 (PB2), U5.15 (PA10)
mcuConnTX: U3.13 (PB1), U5.16 (PA11)
pBJT: R16.2, U5.12 (PA07)
pFET: R14.2, U5.30 (PA21)
pIn: Q1.3 (C), U5.13 (PA08)
pOut: J10.3, Q1.1 (E)
rBJT: R18.2, U5.11 (PA06)
rFET: R23.2, U5.24 (PA15)
rIn: Q2.3 (C), U5.23 (PA14)
rOut: J8.3, Q2.1 (E)

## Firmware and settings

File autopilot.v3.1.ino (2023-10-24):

/*
StratoSoar, an autonomous glider project.
Majortiy of this code was written by myself, Charles Nicholson, 2023. autopilotIMU.vx.x was mostly written by J. Remington.
To use this program, change the values in "settings.h" to your liking.
Then, upload the program "autopilotIMU.vx.x" to a different Arduino.
That Arduino will be hooked up over SoftwareSerial. It will be sending yaw, pitch, temp, and pressure data.
The corresponding data can be used in calculations to move the servos accordingly. 
Two Arduinos are used so the master (this one) can go to sleep in the code and save power.
Sleep in the program "autopilotIMU.vx.x" causes catasrpothic failure, but it is already low power enough so sleep is not needed.
MOSFETs are used in this program to turn the servos on and off to save power. The one I use is the 30N06L, a logic level N-Channel FET.
I also use an NPN BJT (2N3906) to power on and off the PWM line. 
I do this so when the FET is low, ground can't go through the servo PWM (signal) line, which would damage the servo and the Arduino.

NOTE: For proper functionality, make sure the data transmission rate is more than the reading. 
      I.E. sendMs (in autopilotIMU.vx.x) = 1500 and the combined delay in this sketch is equal to 1000 ms.

NOTE: this error message does not effect the performance of the autopilot: "uint8_t requestFrom(uint8_t, uint8_t);".
*/

// #include <TinyGPSPlus.h>
#include <SoftwareSerial.h>
#include <Wire.h>
#include <ServoTimer2_8mhz.h> // Other servo library interferes with SW Serial
#include <avr/wdt.h>
#include <avr/sleep.h>
#include <Narcoleptic.h>
#include "settings.h" // File with settings for the autopilot, change this instead of the code
#include "vars.h" // File with most of the variables

// Creating some objects:
// TinyGPSPlus gps;
// SoftwareSerial ss(RXPin, TXPin);
SoftwareSerial mcuConn(mcuRX, mcuTX);

void setup() {
  /*
  Narcoleptic.disableSPI(); // Wasted power
  
  // Another tweak to lower the power consumption
  ADCSRA &= ~(1<<ADEN); // Disable ADC
  ACSR = (1<<ACD); // Disable the analog comparator
  */
  pinMode(13, OUTPUT);
  pinMode(rudderBJT, OUTPUT);
  pinMode(elevatorBJT, OUTPUT);
  pinMode(rudderFET, OUTPUT);
  pinMode(elevatorFET, OUTPUT);
  Wire.begin();
  Serial.begin(SerialBaud); // Start the Serial communications
  mcuConn.begin(MCUBaud);
  // ss.begin(GPSBaud);
  
  if (needRudder) {
    rudderServo.attach(rudderPin);
  }
  if (needElevator) {
    elevatorServo.attach(elevatorPin);
  }
  if (needParachute) {
    parachute.attach(parachutePin);
  }

  digitalWrite(rudderFET, HIGH); // Turn servo on
  digitalWrite(rudderBJT, LOW); // Turn signal line on
  rudderServo.write(1550); // Equal to 90 degrees
  delay(200);
  digitalWrite(rudderBJT, HIGH);
  digitalWrite(rudderFET, LOW);
  delay(1000);
  digitalWrite(elevatorFET, HIGH); // Turn servo on
  digitalWrite(elevatorBJT, LOW); // Turn signal line on
  elevatorServo.write(1550); // Equal to 90 degrees
  delay(200);
  digitalWrite(elevatorBJT, HIGH);
  digitalWrite(elevatorFET, LOW);
  digitalWrite(13, HIGH);
  delay(250);
  digitalWrite(13, LOW);
  delay(1000);
  digitalWrite(13, HIGH);
  delay(250);
  digitalWrite(13, LOW);
  Serial.println("Everything has initialized and the script starts in 1 second!");
  delay(1000);
}

void loop() {
  if (!landed) {
    /*
    if (gps.location.isValid()) {
      currentLat = gps.location.lat();
      currentLon = gps.location.lng();
    } else {
      currentLat = testLat;
      currentLon = testLon;
    }
    */ 

    currentLat = testLat;
    currentLon = testLon;

    // double distanceMeters = gps.distanceBetween(currentLat, currentLon, targetLat, targetLon);

    /*
    if ((distanceMeters >= 10000) && (gps.altitude.feet() <= 1000)) {
      targetLat = 42.7, targetLon = -71.9; // Change to random nearby coordinates as a back up location if previous location is too far
    }

    if ((distanceMeters >= 50000) && (gps.altitude.feet() <= 5000)) {
      targetLat = 43.7, targetLon = -72.9; // Change to random nearby coordinates as a back up location if previous location is too far
    }
   */

    /*
    if ((distanceMeters <= 100) && gps.location.isValid() && gps.altitude.feet() >= 5000) {
      spiral = true;
      rudderServo.write(145); // Sends into a spin to safely make it's way down   
    }

    if ((distanceMeters <= 100) && gps.location.isValid() && gps.altitude.feet() <= 500) {
      parachute.write(90); // Open the parachute under 500 feet to land 
      landed = true;
    }
    */

    if (!spiral) {
      if (mcuConn.available() >= 6) { // Check to see how many bytes we have to read
        byte yawReceive = mcuConn.read(); // Read the transmitted bytes from autopilotIMU.vx.x
        byte pitchReceive = mcuConn.read();
        byte negativePitch = mcuConn.read();
        byte tempReceive = mcuConn.read();
        byte negativeTemp = mcuConn.read();
        byte pressureReceive = mcuConn.read();

        yaw = int(yawReceive) * 2;  // Convert the received byte back to an integer
        pitch = int(pitchReceive);  // Convert the received byte back to an integer
        temp = int(tempReceive);  // Convert the received byte back to an integer
        pressure = int(pressureReceive) * 500;  // Convert the received byte back to an integer

        if (negativePitch == 1) { // Making some things negative if needed
          pitch = pitch * -1;
        }

        if (negativeTemp == 1) {
          temp = temp * -1;
        }
      }

      turnAngle = turningAngle(currentLat, currentLon, yaw, targetLat, targetLon);

      int servoPositionElevator = pidMagicElevator(); // Change PID values in "settings.h" if you want
      int servoPositionRudder = pidMagicRudder(); // Change PID values in "settings.h" if you want

      digitalWrite(rudderFET, HIGH); // Turning on the servo. servo.detach() saves ~75 mA per servo. MOSFET saves additional ~4 mA per servo.
      digitalWrite(rudderBJT, LOW); // Turning on the servo PWM line
      rudderServo.write(servoPositionRudder);
      delay(200);
      digitalWrite(rudderBJT, HIGH); // Turning off the servo PWM line
      digitalWrite(rudderFET, LOW); // Turning off the servo
      // Turn GPS off
      Narcoleptic.delay(600); // Low power mode. Saves about 3 mA. 
      // Turn GPS on
      digitalWrite(elevatorFET, HIGH); // Turning on the servo. servo.detach() saves ~75 mA per servo. MOSFET saves additional ~4 mA per servo.
      digitalWrite(elevatorBJT, LOW); // Turning on the servo PWM line
      rudderServo.write(servoPositionElevator);
      delay(200);
      digitalWrite(elevatorBJT, HIGH); // Turning off the servo PWM line
      digitalWrite(elevatorFET, LOW); // Turning off the servo
      Serial.print("Turning Angle: ");
      Serial.print(turnAngle);
      Serial.print(", Heading: ");
      Serial.print(yaw);
      Serial.print(", Pitch: ");
      Serial.print(pitch);
      Serial.print(", Rudder Servo position: ");
      Serial.print(servoPositionRudderDegrees);
      Serial.print(", Elevator Servo position: ");
      Serial.println(servoPositionElevatorDegrees);

      // speedMPH = gps.speed.mph(); // GPS speed (idk how accurate it is, though it probably is when moving fast-ish in a straight manner)

      /*
      if (speedMPH <= 5) {
        elevatorServo.write(115); // Dive down when stalled
      }
      */
    
      // This saves to an external EEPROM (AT24Cx) so we can get some yummy data
      if (runEEPROM) { 
        writeToEEPROM(eepromI2CAddress, eepromAddress, int(yaw / 2));
        delay(10);
        eepromAddress++;  
        writeToEEPROM(eepromI2CAddress, eepromAddress, pitch); 
        delay(10);
        eepromAddress++;  
        writeToEEPROM(eepromI2CAddress, eepromAddress, int(temp));
        delay(10);
        eepromAddress++;
        writeToEEPROM(eepromI2CAddress, eepromAddress, int(pressure/500)); 
        delay(10);
        eepromAddress++;
        if (eepromAddress >= maxAddress) {
          runEEPROM = false;
        }
      }
    } 
  } 
}

// loop is now over, on to the boring functions that nobody cares about

double deg2rad(double deg) {
  return deg * pi / 180.0;
}

double rad2deg(double rad) {
  return rad * 180.0 / pi;
}

double turningAngle(double currentLat, double currentLon, double heading1, double targetLat, double targetLon) {
  double a = azimuth(currentLat, currentLon, targetLat, targetLon);
  double h = deg2rad(heading1);
  double angle = a - h;
  if (angle < -pi) angle += 2 * pi;
  if (angle > pi) angle -= 2 * pi;
  return rad2deg(angle);
}

double azimuth(double currentLat, double currentLon, double targetLat, double targetLon) {
  double dLon = deg2rad(targetLon - currentLon);
  double dPhi = log(tan(deg2rad(targetLat) / 2 + pi / 4) / tan(deg2rad(currentLat) / 2 + pi / 4));
  if (fabs(dLon) > pi) {
      dLon = dLon > 0 ? -(2 * pi - dLon) : (2 * pi + dLon);
  }
  return fmod((atan2(dLon, dPhi) + 2 * pi), (2 * pi));
}

void writeToEEPROM(byte EEPROMAddress, byte dataAddress, byte dataValue) {
  Wire.beginTransmission(EEPROMAddress);
  Wire.write(dataAddress);
  Wire.write(dataValue);
  Wire.endTransmission();
  delay(5);
}

int pidMagicElevator() {
  // Calculate the error
  errorElevator = setpointElevator - pitch; 

  // Calculate the outputElevator
  int outputElevator = KpElevator * errorElevator + KiElevator * integralElevator + KdElevator * (errorElevator - prevErrorElevator); // PID math wizardy

  // Apply the outputElevator to the servo
  servoPositionElevatorDegrees = 90 - outputElevator;  // Adjust servo position based on the outputElevator

  // Update previous error and integral
  prevErrorElevator = errorElevator;
  integralElevator += errorElevator;

  int servoPositionElevatorNew = map(servoPositionElevatorDegrees, 0, 180, 750, 2250); // 750, 2250

  return servoPositionElevatorNew;
}

int pidMagicRudder() {
  setpointRudder = yaw + turnAngle;
  inputRudder = yaw;

  // Calculate the error
  errorRudder = setpointRudder - yaw;

  // Calculate the control output
  int outputRudder = KpRudder * errorRudder + KiRudder * integralRudder + KdRudder * (errorRudder - prevErrorRudder);

  // Apply the control output to the servo
  servoPositionRudderDegrees = 90 + outputRudder;  // Adjust servo position based on the output

  // Update previous error and integral
  prevErrorRudder = errorRudder;
  integralRudder += errorRudder;

  int servoPositionRudderNew = map(servoPositionRudderDegrees, 0, 180, 1250, 1750); // 750, 2250

  return servoPositionRudderNew;
}

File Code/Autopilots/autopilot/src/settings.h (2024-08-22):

/*
settings.h, part of StratoSoar MK2, for an autonomous glider.
Copyright (C) 2024 Charles Nicholson

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
You should have received a copy of the GNU General Public License
along with this program.  If not, see <https://www.gnu.org/licenses/>.
*/

#pragma once

// Change this file to match your needs.

// Enables.
#define DEVMODE // Toggle the serial monitor on and off.
// #define LOW_POWER  // Activates low power mode. GPS will be lower power among others. Note that the serial monitor will no longer work.
#define TEST_COORD // Use testing coordinates.
// #define CHANGE_TARGET // If the target location is too far away, change it to some place closer.
#define SPIN_STOP // Land the glider by sending it into a spin.
// #define STALL_STOP // Experimental, may be unsupported. Do not use. Land the glider by repeatedly stalling it.
// #define NEED_PARACHUTE // Enable the parachute servo.
// #define NEED_ELEVATOR // Enable the elevator servo.
#define NEED_RUDDER // Enable the rudder servo.
// #define DIVE_STALL    // Dive down when speed gets too low.
#define USE_EEPROM // Toggle the usage of the EEPROM.
// #define WIRELESS   // Experimental. If an HCO5 module is attached, a wireless serial connection can be made. More information in the docs.
// #define EEPROM_BUTTON // If enabled, the EEPROM will run for a configurable number of cycles after being pressed by a button. It will also record more data.
// #define GROUND // If doing ground testing, use this to enable faster updates.
// #define ERASE_EEPROM  // If enabled, the EEPROM will be erased before every flight. This is not recommended.
// #define SERVO_NONBLOCKING // Experimental, do not use.
// #define DROP_START // Starts the operations when a decreasing altitude is detected.

// Time settings.
#define FAST_UPDATE_PERIOD 3600   // In this time, the glider will update its yaw more frequently. The time is in seconds.
#define GPS_SLEEP 10000           // This is how long the glider will wait until it will get a new GPS fix, saving power in between fixes. The time is in milliseconds and does not apply if ground is enabled.
#define GPS_GROUND_SLEEP 10000    // This is how long the glider will wait until it will get a new GPS fix, saving power in between fixes. The time is in milliseconds and does not apply if ground is disabled.
#define SPIRAL_SLEEP 500          // If spiraling down, how long should the glider sleep for in between GPS and parachute checkups?
#define BELOW_THRESHOLD_SLEEP 500 // If the yaw is below the threshold, the glider will sleep for this many seconds before checking if the drift is enough.
#define ABOVE_THRESHOLD_SLEEP 500 // If the yaw is above the threshold, the glider will sleep for this long. Note that 200 will be subtracted from this because there was a 200 ms delay in between moving servos.
#define ABV_THRS_FST_UPDT_SLP 500 // (Above threshold fast update period sleep). If the yaw is above the threshold and if the glider is in the fast update period of flight, the glider will for this long. Same note as above, too.
#define FLIGHT_TIME 240           // In minutes, the time expected to be in flight for, used for calculating the time between EEPROM writes.

// Other settings.
#define SETPOINT_ELEVATOR 10   // Desired pitch angle (in degrees).
#define TOO_SLOW 5             // If DIVE_STALL is defined, and the MPH is equal to or below this threshold, dive down.
#define YAW_DFR_THRESHOLD 5    // The threshold needed to move the servos.
#define ARM_ALT 10             // Meters before the altitude is considered safe to arm the glider if DROP_START is enabled.
#define SPIN_DEGREE 180        // The angle of the servo when spiraling down to the ground. 90 degrees is the middle.
#define REF_PRESSURE 101659.39 // Daily pressure at sea level today in Pa.

// Threshold for parachute and spiraling.
#define PARACHUTE_ALT_THRESHOLD 500 // If the glider is under this, and the distance is less than PARACHUTE_DST_THRESHOLD, open the parachute.
#define PARACHUTE_DST_THRESHOLD 100 // If the glider is under PARACHUTE_ALT_THRESHOLD, and the distance is less than this, open the parachute.
#define SPIRAL_ALT_THRESHOLD 0      // If the glider is above this, and the distance is less than SPIRAL_DST_THRESHOLD, spiral the glider down.
#define SPIRAL_DST_THRESHOLD 30     // If the glider is above SPIRAL_ALT_THRESHOLD, and the distance is less than this, spiral the glider down.
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

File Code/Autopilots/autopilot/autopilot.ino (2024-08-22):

// WARNING:
// This is still a work in progress! Code may not work!

/*
autopilot.ino, part of StratoSoar MK2, for an autonomous glider.
Copyright (C) 2024 Charles Nicholson

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
You should have received a copy of the GNU General Public License
along with this program.  If not, see <https://www.gnu.org/licenses/>.
*/

// https://github.com/crnicholson/StratoSoar-MK2/.

#include "SparkFun_External_EEPROM.h" // Click here to get the library: http://librarymanager/All#SparkFun_External_EEPROM
#include <ArduinoLowPower.h>
#include <Servo.h>
#include <SparkFun_u-blox_GNSS_v3.h> // http://librarymanager/All#SparkFun_u-blox_GNSS_v3.
#include <Wire.h>

#include "src/settings.h"
#include "src/utils.h"

// PID variables.
float setpointRudder, inputRudder, errorRudder, prevErrorRudder, integralRudder, inputElevator, errorElevator, prevErrorElevator, integralElevator;

// Other variables.
int yawDifference, nowEEPROM, flightNumber, cycles, previous, averageAlt, oldAverageAlt, oldAlt, oldestAlt, dropCounter, lastYaw = 361;
long eepromAddress, startTimer, endTimer, eepromSize, averageWrite, now, ms, last, nowGPS, msGPS, lastGPS, lastEEPROM, pi = 3.14159265358979323846;
float writeTime;
bool spiral, dropped, inFastEEPROM, runEEPROM = true, fastUpdatePeriod = true, firstEEPROM = true, firstLoopForDropDetect = true;

struct __attribute__((packed)) dataStruct {
  float lat;
  float lon;
  int alt;    // GPS altitude.
  int bmeAlt; // BME280 altitude.
  int sats;
  int fixType;
  int speed;
  int seconds;
  int minutes;
  int hours;
  int day;
  int month;
  int year;
  float temp;     // In Celsius.
  float pressure; // In hPa (millibar).
  float humidity; // Relative humidity.
  int yaw;
  int pitch;
  int roll;
  int servoPositionElevator;
  int servoPositionRudder;
  float volts;
  float turnAngle;
  float distanceMeters;
  float hdop;
} data;

struct __attribute__((packed)) dataStructIMU {
  float pitch;
  float roll;
  float yaw;
  long temp;
  float pressure;
  long humidity;
} receivedData;

SFE_UBLOX_GNSS gps;    // Initialize GPS.
ExternalEEPROM eeprom; // Initialize EEPROM.

void setup() {
  pinMode(LED, OUTPUT);
  pinMode(ERR_LED, OUTPUT);
  pinMode(RUDDER_BJT, OUTPUT);
  pinMode(ELEVATOR_BJT, OUTPUT);
  pinMode(PARACHUTE_BJT, OUTPUT);
  pinMode(RUDDER_FET, OUTPUT);
  pinMode(ELEVATOR_FET, OUTPUT);
  pinMode(PARACHUTE_FET, OUTPUT);
  pinMode(WAKEUP_PIN, OUTPUT);
  pinMode(FALSE_WAKEUP_PIN, INPUT);
  pinMode(BAT_VOLTAGE_PIN, INPUT);
  pinMode(WRITE_PIN, OUTPUT);
  pinMode(BUTTON, INPUT_PULLUP);
  digitalWrite(LED, LOW);
  digitalWrite(ERR_LED, LOW);
  digitalWrite(RUDDER_BJT, HIGH);
  digitalWrite(ELEVATOR_BJT, HIGH);
  digitalWrite(PARACHUTE_BJT, HIGH);
  digitalWrite(RUDDER_FET, LOW);
  digitalWrite(ELEVATOR_FET, LOW);
  digitalWrite(PARACHUTE_FET, LOW);
  digitalWrite(WAKEUP_PIN, LOW);
  digitalWrite(WRITE_PIN, LOW);
  Wire.begin();

  longPulse(LED, 0);     // Pulse LED to show power up.
  longPulse(ERR_LED, 0); // Testing the error LED, too.

#ifdef DEVMODE
  SerialUSB.begin(SERIAL_BAUD_RATE); // Start the serial monitor.
  while (!SerialUSB) {
    longPulse(ERR_LED, 0); // Wait for serial to connect.
  }

  delay(1000);

  SerialUSB.println("StratoSoar MK2.x Flight Controller");
#endif

  Serial1.begin(BAUD_RATE); // Hardware serial connection to the ATMega and the IMU.

  longPulse(LED, 0); // Signal that the sketch is starting.
  longPulse(ERR_LED, 0);

  I2CScan(); // This will long pulse the LED if there is an error.

#ifdef USE_EEPROM
  eeprom.setMemoryType(512); // Valid types: 0, 1, 2, 4, 8, 16, 32, 64, 128, 256, 512, 1025, 2048

  if (eeprom.begin() == false) {
#ifdef DEVMODE
    SerialUSB.println("No EEPROM detected. Freezing sketch.");
#endif
    while (1)
      longPulse(ERR_LED, 0);
  }

  eepromSize = eeprom.length();
#ifdef DEVMODE
  SerialUSB.println("EEPROM detected!");
  SerialUSB.print("EEPROM size in bytes: ");
  SerialUSB.println(eepromSize);
#endif
#ifdef ERASE_EEPROM
#ifdef DEVMODE
  SerialUSB.println("Erasing EEPROM, should take ~10 seconds.");
#endif
  startTimer = millis();
  eeprom.erase();
  endTimer = millis();
#ifdef DEVMODE
  SerialUSB.print("Done erasing. Time took in milliseconds: ");
  SerialUSB.println(endTimer - startTimer);
#endif
#endif

  eeprom.write(0, 200); // Testing EEPROM.

#ifdef DEVMODE
  SerialUSB.println("Testing EEPROM.");
  SerialUSB.print("EEPROM reads (should be 200): ");
  SerialUSB.println(eeprom.read(0));
#endif
  if (eeprom.read(0) != 200) {
#ifdef DEVMODE
    SerialUSB.println("Warning: EEPROM is not working as expected. Try removing the average write time finder from the code.");
#endif
    longPulse(ERR_LED, 0);
  }
#endif

#ifdef NEED_RUDDER
  rudderServo.attach(RUDDER_PIN);
#endif
#ifdef NEED_ELEVATOR
  elevatorServo.attach(ELEVATOR_PIN);
#endif
#ifdef NEED_PARACHUTE
  parachute.attach(PARACHUTE_PIN);
#endif

#ifdef NEED_RUDDER
#ifdef DEVMODE
  SerialUSB.println("Moving rudder to 90 degrees.");
#endif
  moveRudder(90, 0); // Move the rudder to 90 degrees.
#endif
#ifdef NEED_ELEVATOR
  moveElevator(90, 0); // Move the elevator to 90 degrees.
#endif

#ifndef TEST_COORD
  if (gps.begin() == false) { // Connect to the u-blox module using Wire port.
#ifdef DEVMODE
    SerialUSB.println(F("u-blox GNSS not detected at default I2C address. Please check wiring. Freezing."));
#endif
    while (1)
      longPulse(ERR_LED, 0);
  }

  // gps.hardReset(); // Hard reset - force a cold start. This will wipe any data in the GPS - almost never use this.

  gpsConfig(); // This will long pulse LED if there is an error.

  waitForFix();
#endif

  delay(1000);

#ifdef DEVMODE
  SerialUSB.println("Everything has initialized and the script starts in 10 seconds.");
#endif

  delay(10000);

  writeTime = (FLIGHT_TIME * 60) / (eepromSize / BYTES_PER_CYCLE) + EEPROM_BUFFER;

  SerialUSB.println(writeTime);

  startTimer = millis();
  last = startTimer;
}
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

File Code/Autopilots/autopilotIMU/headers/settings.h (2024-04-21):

/*
settings.h, part of StratoSoar MK2, for an autonomous glider.
Copyright (C) 2024 Charles Nicholson

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
You should have received a copy of the GNU General Public License
along with this program.  If not, see <https://www.gnu.org/licenses/>.
*/

// Pins.
#define RX 10       // TX pin of the mcuConn for communicating with the SAMD.
#define TX 9        // RX pin of the mcuConn for communicating with the SAMD.
#define WRITE_PIN 2 // Pin that connects to SAMD to know when to send data.
#define LED 13      // Pin that connects to an external status LED.

#define BAUD_RATE 9600        // Baud rate for the mcuConn.
#define SERIAL_BAUD_RATE 9600 // Baud rate for the serial monitor.
#define Kp 30.0               // These are the free parameters in the Mahony filter and fusion scheme, Kp for proportional feedback, Ki for integral.
#define Ki 0.0                // With MPU-9250, angles start oscillating at Kp = 0. Ki does not seem to help and is not required.
#define MAG_DEC 14.5          // Conventional nav, yaw increases CW from North, corrected for local magnetic declination. Find yours here: http://www.ngdc.noaa.gov/geomag-web/#declination.
#define BME_ADDRESS 0x76      // Address of the BME280 sensor.
// #define DEVMODE               // Comment to stop the use of the serial monitor.

// Accel offsets and correction matrix.
float A_B[3]{539.75, 218.36, 834.53};
float A_Ainv[3][3]{
    {0.51280, 0.00230, 0.00202},
    {0.00230, 0.51348, -0.00126},
    {0.00202, -0.00126, 0.50368}};

// Mag offsets and correction matrix.
float M_B[3]{18.15, 28.05, -36.09};
float M_Ainv[3][3]{
    {0.68093, 0.00084, 0.00923},
    {0.00084, 0.69281, 0.00103},
    {0.00923, 0.00103, 0.64073}};

float G_off[3] = {-299.7, 113.2, 202.4}; // Raw offsets, determined for gyro at rest.

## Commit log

2023-12-19 Update IMU
2024-02-08 Add I2C scan and warning
2024-02-23 Rename samdFlightController.kicad_pcb to PCB + Schematic/samdFlightController.kicad_pcb
    [samdFlightController.kicad_pcb]
2024-02-23 Rename samdFlightController.kicad_pro to PCB + Schematic/samdFlightController.kicad_pro
2024-02-23 Rename samdFlightController.kicad_sch to PCB + Schematic/samdFlightController.kicad_sch
    [samdFlightController.kicad_sch]
2024-02-23 Rename glider v33.f3z to 3D Files/glider v33.f3z
    [glider v33.f3z]
2024-02-23 Rename partsForGlider v4.stl to 3D Files/partsForGlider v4.stl
    [partsForGlider v4.stl]
2024-03-25 Update IMU calibration
2024-04-10 Got servos working
2024-04-20 Finish new PCB
    [StratoSoar-MK2.2.kicad_pcb, StratoSoar-MK2.2.kicad_sch]
2024-04-21 Update servo
2024-05-06 PCB, Code
    [StratoSoar MK2.2.step, StratoSoar-MK2.2.kicad_pcb, bom.csv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]
2024-05-06 Fix minor issue with fast update period
    [autopilot.ino, settings.h]
2024-05-06 Fix fast update period
    [autopilot.ino, settings.h]
2024-05-07 Fix some other bugs!
    [autopilot.ino, settings.h]
2024-05-10 Add 3D files
    [StratoSoar Rev2 v26 Cockpit.3mf, StratoSoar Rev2 v26.3mf, StratoSoar Rev2 v26_StratoSoar Rev2 v26_Cockpit_1_Bottom half.obj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]
2024-06-17 Cleaned up 3D files
    [StratoSoar Rev2 v26 Cockpit.3mf, StratoSoar Rev2 v26.3mf, StratoSoar Rev2 v26_StratoSoar Rev2 v26_Cockpit_1_Bottom half.obj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]
2024-06-17 Working on a fix
    [autopilot.ino, settings.h, utils.ino]
2024-06-18 3D files
    [StratoSoar Rev2 v36_StratoSoar Rev2 v36_Bumper_1_Body1.stl, StratoSoar Rev2 v36_StratoSoar Rev2 v36_Horizontal mount_1_Horizontal mount.stl, StratoSoar Rev2 v3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]
2024-07-17 Finishing touches before launch
    [noseCone.stl]

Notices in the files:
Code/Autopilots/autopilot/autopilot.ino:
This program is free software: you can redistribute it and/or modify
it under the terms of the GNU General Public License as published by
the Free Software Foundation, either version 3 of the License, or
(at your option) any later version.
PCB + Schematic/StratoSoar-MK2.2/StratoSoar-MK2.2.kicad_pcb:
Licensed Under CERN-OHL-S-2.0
